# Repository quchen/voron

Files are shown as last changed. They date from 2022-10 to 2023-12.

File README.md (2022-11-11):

# Voron 2.4

This is my config for my 3D printer, a Voron 2.4r2, 250mm size.

For pretty (and not so pretty) pictures, look at buildlog.md.

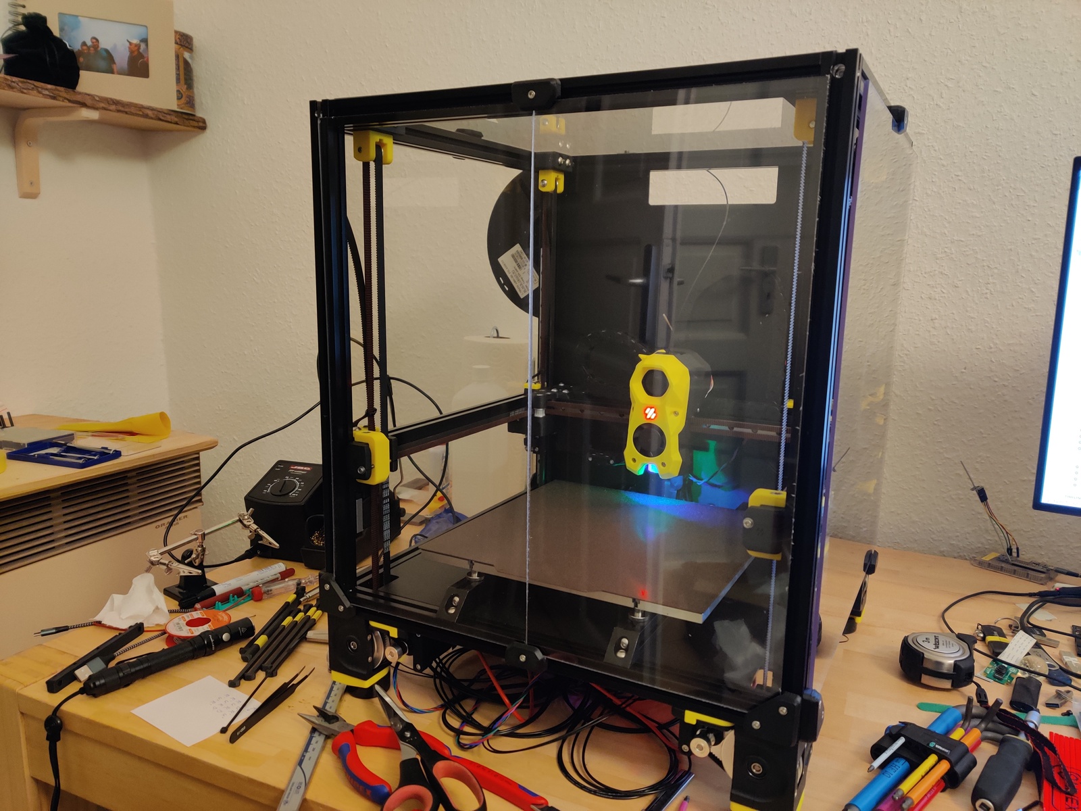
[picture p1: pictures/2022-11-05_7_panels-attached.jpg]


## Table of contents

- [config/](config/)         Printer configuration files.
- [manuals/](manuals/)       Assembly, circuitry, etc.
- [mods/](mods/)             Addons for the printer.
- [pictures/](pictures/)     Pictures for the buildlog.
- [buildlog.md](buildlog.md) Buildlog for everything I’ve done on the printer,
                             including time estimates.

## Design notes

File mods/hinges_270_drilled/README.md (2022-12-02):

https://github.com/VoronDesign/VoronUsers/tree/master/printer_mods/chrisrgonzales/270_degree_hinge

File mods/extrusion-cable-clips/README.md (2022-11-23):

# Extrusion cable clips

I use these to hide my motor cables in the back of the gantry.

https://www.thingiverse.com/thing:2246832

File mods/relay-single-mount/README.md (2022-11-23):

# Relay mount

This one was given to me by a friend. The holes in the relay PCB are too small
though so it doesn’t quite fit :-(

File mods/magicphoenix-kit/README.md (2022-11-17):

# MagicPhoenix Voron kit parts

Some custom parts for e.g. the breakout PCB.

https://github.com/MagicPhoenix/MPX-VORON-24R2-KIT/tree/main/Printed%20Parts

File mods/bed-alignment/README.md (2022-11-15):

# Easy bed alignment tools

Why didn’t I use those in the build!

https://github.com/VoronDesign/VoronUsers/tree/master/printer_mods/GadgetAngel/Bed_Support_Alignment_Tools

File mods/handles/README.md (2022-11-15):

# Handles for picking up the Voron

https://github.com/VoronDesign/VoronUsers/tree/master/printer_mods/jeoje/Sturdy_Handles

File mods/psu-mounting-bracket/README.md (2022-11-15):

# Meanwell 24V PSU holder

https://github.com/VoronDesign/VoronUsers/tree/master/printer_mods/aTinyShellScript/RS_PSU_DIN_Brackets

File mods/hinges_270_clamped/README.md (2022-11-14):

https://github.com/VoronDesign/VoronUsers/tree/master/printer_mods/AlexanderT-Moss/270-Clamping-Hinges

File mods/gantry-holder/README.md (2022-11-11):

# Gantry holder

These sticks allow hanging the gantry on the top of the frame. Useful to work at
its bottom, e.g. to change the gantry supports. They also ensure the gantry is
at the same height on all sides.

https://github.com/VoronDesign/VoronUsers/tree/master/printer_mods/tallman5/z-locks

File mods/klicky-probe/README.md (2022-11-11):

# Klicky probe

https://github.com/jlas1/Klicky-Probe/tree/main/Printers/Voron/v1.8_v2.4_Legacy_Trident/v1.8_v2.4_Legacy_Trident_STL

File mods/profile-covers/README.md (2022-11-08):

# Profile covers

- https://github.com/VoronDesign/VoronUsers/tree/master/printer_mods/chri.kai.in/20x20mm_Profile_Covers
- https://github.com/VoronDesign/VoronUsers/tree/master/printer_mods/filotto78/6mm_slot_cover

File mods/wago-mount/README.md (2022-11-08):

# Wago mounts

Not much to say. Wago clamps are cool.

https://github.com/VoronDesign/VoronUsers/tree/master/printer_mods/LoganFraser/WagoMounts

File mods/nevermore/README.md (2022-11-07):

# Nevermore

Don’t like cancer because of toxic styrene in your lungs? Lucky you are!

- Printed: Standard version (not XL)
- Git hash: 10ec5e9e80064c5ac2ecf3905a2cfe98cf476909 (2022-11-06)
- Git: git@github.com:nevermore3d/Nevermore_Micro.git
- Github: https://github.com/nevermore3d/Nevermore_Micro

# Official readme

Four parts; Plenum+Lid, and Cartridge+Lid.

Choose between regular and XL cartridge. XL is just 10mm longer, which can make
a big difference in air flow.

Choose XL for max carbon content and filter duration, and if you don't mind the
fan (200Pa+) has to run faster/noisier. You probably have to use pellets instead
of granular carbon too.

Choose regular if you have granular carbon and/or a weaker fan, and/or wish to
have a more silent experience. Regular also allows for somewhat higher airflow,
which could make a small difference compared to XL in chamber heat up times.

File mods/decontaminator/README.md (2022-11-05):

# Decontaminator

Wipes the nozzle before printing to remove all the gunk.

https://github.com/VoronDesign/VoronUsers/tree/master/abandoned_mods/printer_mods/edwardyeeks/Decontaminator_Purge_Bucket_%26_Nozzle_Scrubber

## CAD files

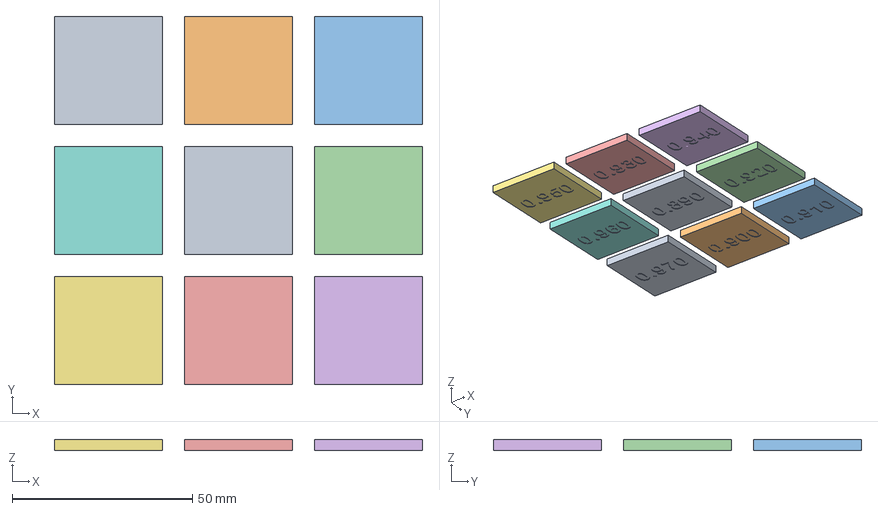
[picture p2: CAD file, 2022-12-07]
config/calibration/extrusion-multiplier-andrew-ellis.3mf
102.0 x 102.0 x 3.00 mm
EM_Cube-0.890.stl
EM_Cube-0.900.stl
EM_Cube-0.910.stl
EM_Cube-0.920.stl
EM_Cube-0.930.stl
EM_Cube-0.940.stl
EM_Cube-0.950.stl
EM_Cube-0.960.stl
EM_Cube-0.970.stl

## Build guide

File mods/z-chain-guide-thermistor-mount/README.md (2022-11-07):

# Z Chain Guide Thermistor Mount

https://github.com/VoronDesign/VoronUsers/tree/master/printer_mods/jeoje/Z_Chain_Guide_Thermistor_Mount

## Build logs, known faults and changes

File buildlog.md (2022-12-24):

# Voron 2.4 buildlog

This is a technical diary AKA buildlog of me assembling a Voron 2.4r2, 250mm
version.

I try to add annotations where I make mistakes, but in general it’s good to
double-check whether things I’ve described in a step are a good idea before
copying them.

# 2022-10-25

Package arrived. Got Pif parts in blue and yellow.

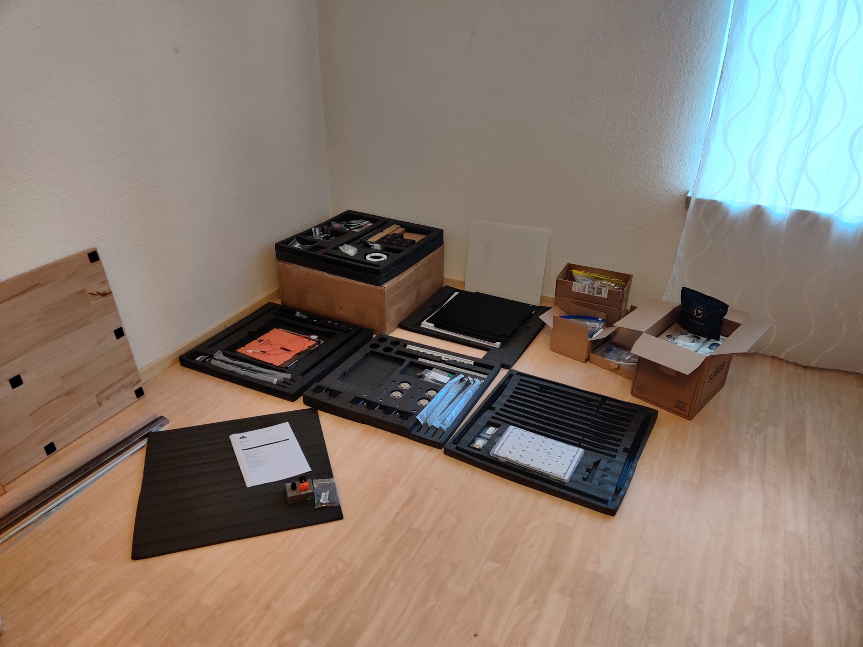
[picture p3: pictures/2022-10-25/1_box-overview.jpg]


Around 1m² of desk space cleaned, my trusty Prusa 2.5 went onto the gas oven
(turned off). Build area cleaned, let’s go!

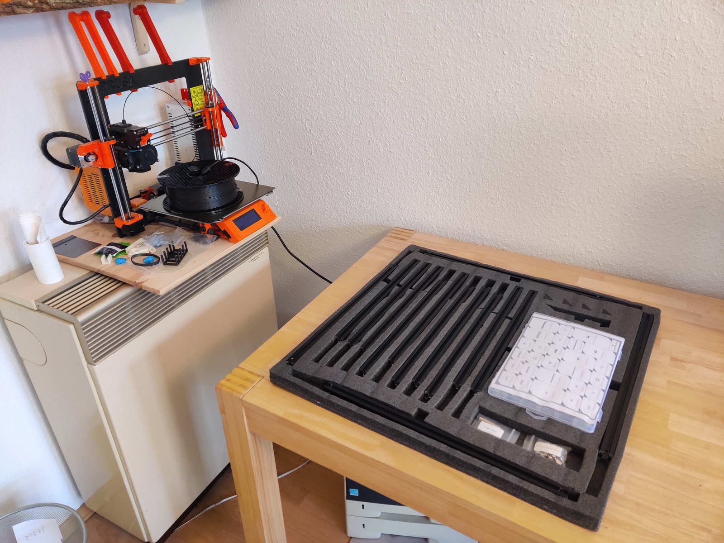
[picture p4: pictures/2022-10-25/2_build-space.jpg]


Time: 15min

Downloaded the build manual for Voron (and Stealthburner for later). Initialize
this Git repo. 5min

## Frame assembly

Extrusions sorted and labeled. 10min

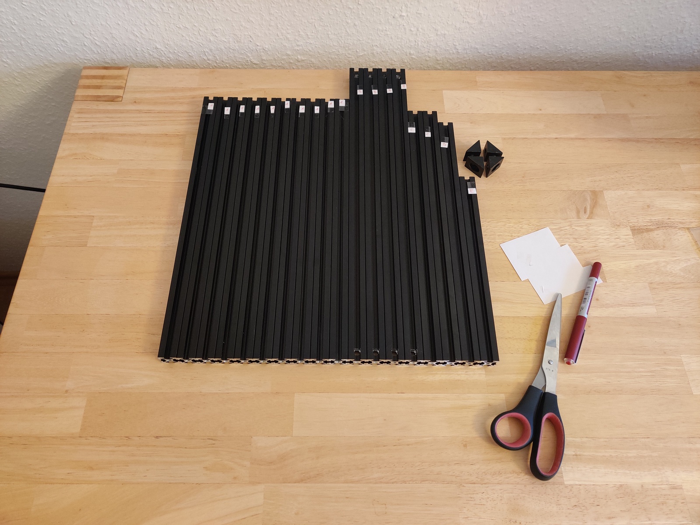
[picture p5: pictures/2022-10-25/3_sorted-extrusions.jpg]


Adding screws to A extrusions. I remember my friend telling me about the _frame
spring fasteners_ that they forgot initially. Time to open the
[MagicPhoenix manual](http://mpx.wiki/) as well! Yup, use (non-standard) frame
spring fasteners.

30min later, cube almost finished, forgot thread locker. Fuck. Anyway, time
to get the DIN angle for fine tuning, and the thread locker. Undo all the screws
again. Need to go boudlering though, and threadlocker would set a time limit on
assembly and squaring. Stopping frame assembly for now.

15min of unpacking linear rails, finding a suitable glass, and putting the
sliders into IPA. Now I will go bouldering for real, promise.

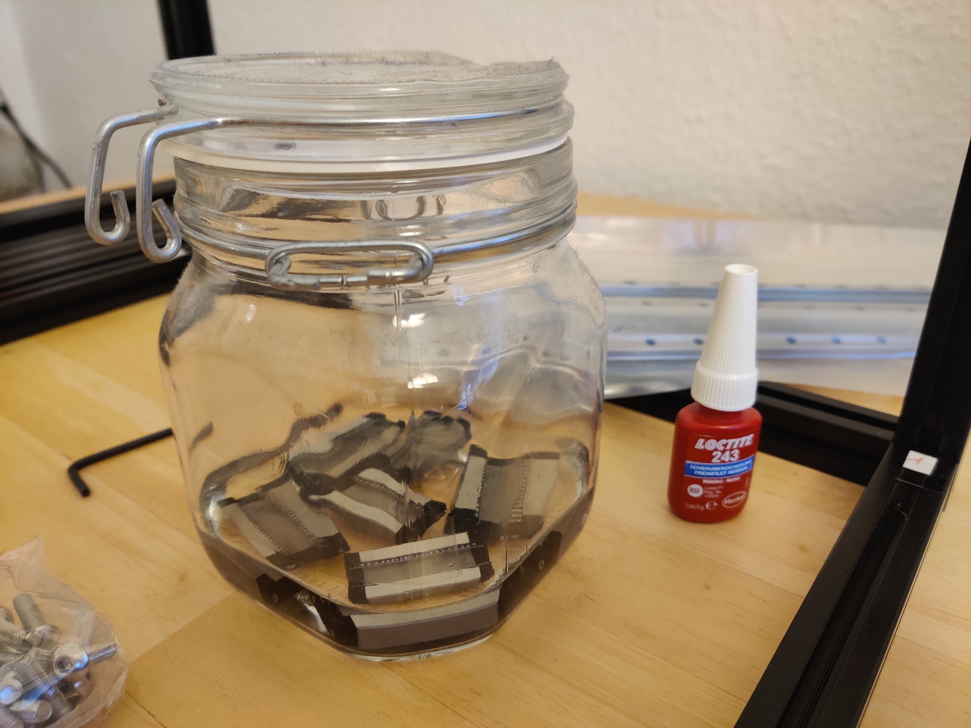
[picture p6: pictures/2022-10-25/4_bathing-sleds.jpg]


Time taken: 1h, total 1h15m.

Reassembled the linear rails while drenching them in IPA. Did not expect the
MGN9H to be _that_ hard to get on the rail, MGN12H is a piece of cake in
comparison. Some balls jumped out, reinserting them is super finnicky. Keeping
them on-rail in IPA for a bit longer, and will move them on occasion. Speaking
of movement, only one of the rails is good (sled moves under its own weight),
the rest is average, except for one of the MGN9H, which is quite stiff. Maybe
upgrade to Hiwin later (for a hefty premium …). 20min for this.

Another 45min later, the frame is fully assembled, and all corners are
electrically connected (diamond filing the contact surfaces). Used a DIN norm
angle to make sure the mechanical assembly is flush. Upper/lower Diagonals are
all 579mm, left/right/front/back ones 594mm without further adjustment. Kudos
to the precision work by MagicPhoenix! Used my DIN angle to check for 90°; most
angles are perfect, some are a tiny bit off so that I can
audibly-but-not-visibly move the angle. Good enough.

I decided against using threadlocker for the frame, because Loctite cures in
around 10-20min, which would not have let me adjust the screws if things
hadn’t gone to plan. Might add Loctite later screw-by-screw when more things
hold the frame in place, but only if problems occur. Screws are tight so that
when I use the hex key with the worse lever, my finger hurts when turning them.

Installed the heat bed rails by estimating the center of the bed with a tape
measure, and going from there with the caliper. Distance between the extrusions
is 130mm±<0.2mm, way more accurate than I need. I do have an offset by 0.5mm to
the left though, which I will worry about when installing the bed, which should
give me much more practical guidance. **Note from the future:** there is a
[simple alignment helper mod][bed-rails-alignment] that would have made this
much easier.

[bed-rails-alignment]: https://github.com/VoronDesign/VoronUsers/tree/master/printer_mods/GadgetAngel/Bed_Support_Alignment_Tools

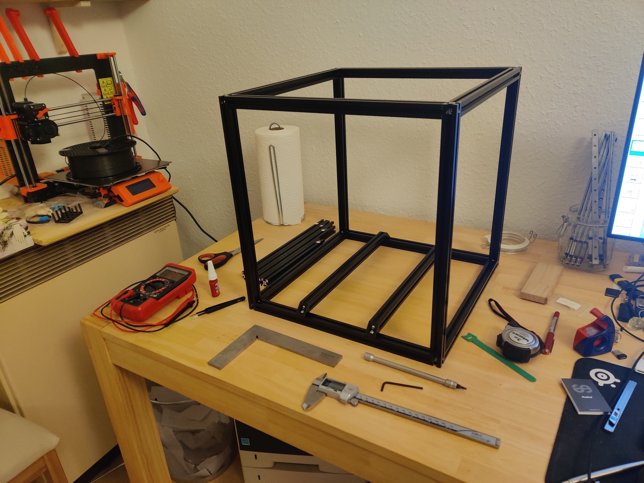
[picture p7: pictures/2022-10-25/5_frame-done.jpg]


Time taken: 1h45m, for a total of 3h so far.

# 2022-10-26: Frame and gantry

## Z linear rails

Spent 15 minutes greasing the rails with standard grease. It’s quite hard to get
it in there, the syringe tip didn’t work (inject it from below through a rail
hole). Just made a little mess and hoped enough would be on the bearings.

The next 45min I installed the rails. I got one nut the wrong way round; it’s
not noticeable but _I know_. It’ll be my secret. Nothing special here, just
juggling with Loctite hardening, and aligning them quick enough. The plastic
rail adjustment clamps are a blessing. Oh and my Yubikey is 3.5mm thick, so I
used that as a spacer for the gap at the bottom of the Z rails. **Note from 50h
in the future:** A bigger gap makes it easier to insert covers later. There is
zero need to have the carriages go that deep. Make it 5mm or even 10mm!

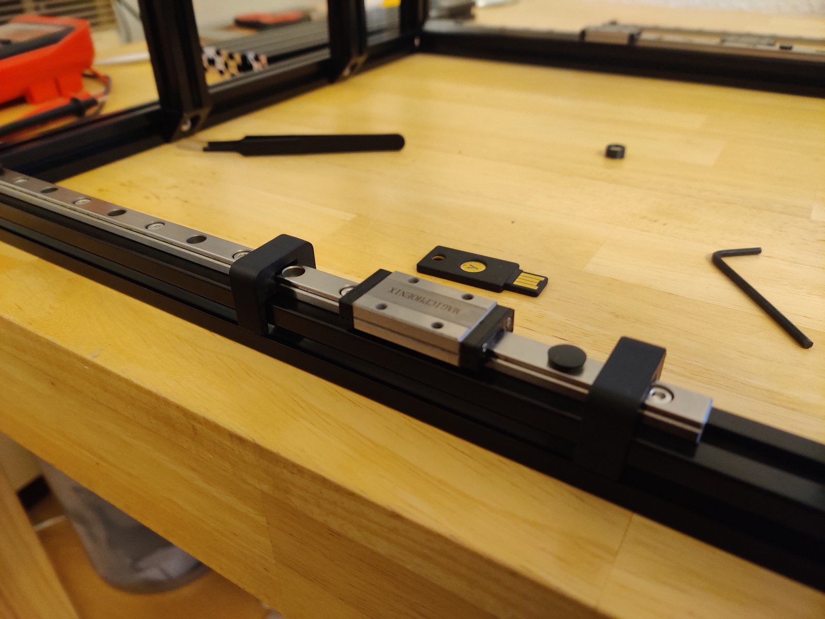
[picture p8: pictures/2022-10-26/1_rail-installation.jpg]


# DIN rails

15 minutes for installing the floor and DIN rails. Initially I installed the
rails parallel to the bed rails, but they actually have to be perpendicular.
Takes a minute to change that though, so no problem.

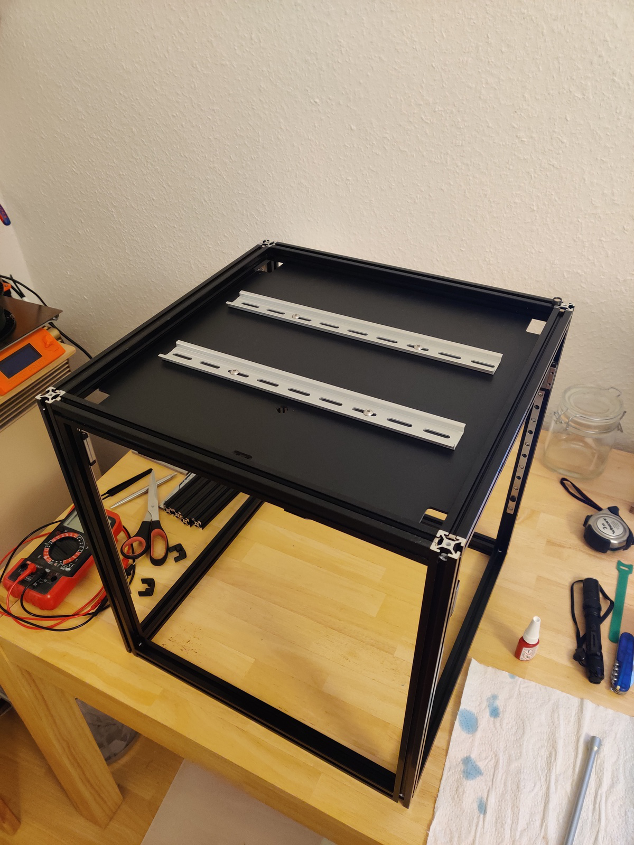
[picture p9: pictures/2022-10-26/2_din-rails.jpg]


The next 30 minutes were pure bliss: heat inserts. It’s amazing. I hope there
are many more. 250 °C on the soldering iron, slowly pushing it in, then flushing
the surface with a flat piece of plastic for a couple of seconds. All inserts
are _perfect_. I’m proud.

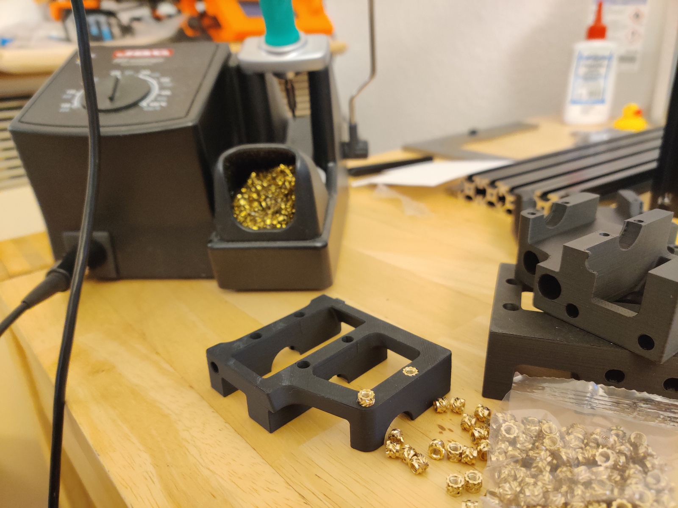
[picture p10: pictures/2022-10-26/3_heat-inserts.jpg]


The first foot for the frame to stand on took 45 minutes. A couple of small
mistakes were easy to remedy, namely I screwed the foot onto the wrong side of
the frame, and also I forgot including the M5 nut for the plastic foot’s foot to
be fastened to. Neither took more than a minute to fix.

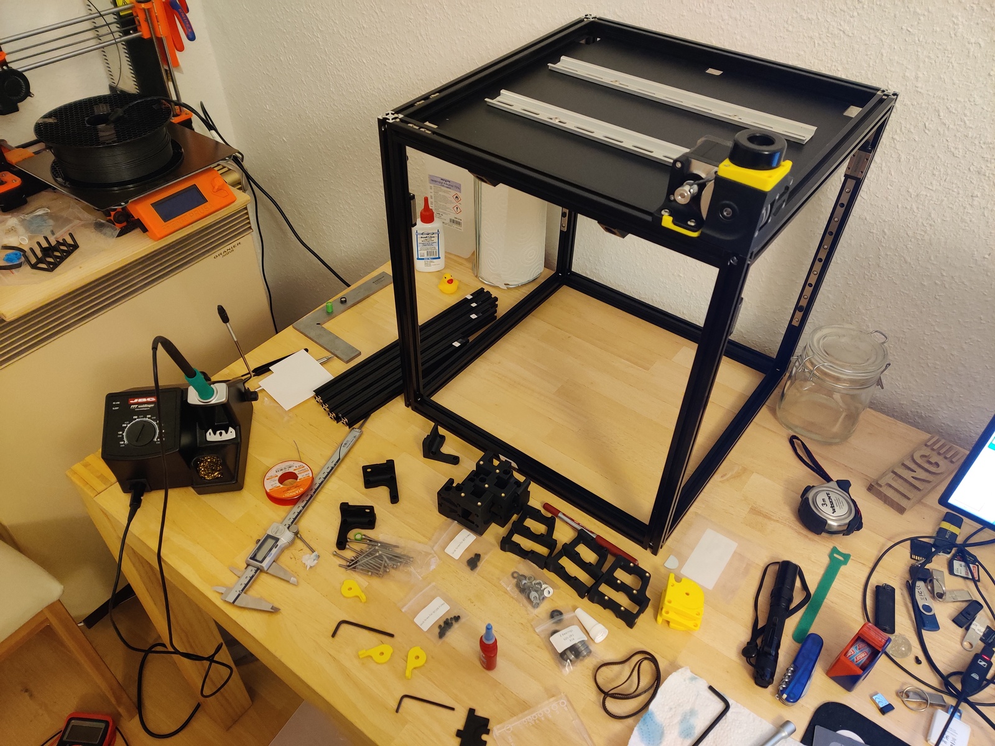
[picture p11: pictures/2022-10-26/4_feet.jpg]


Eyedler are super easy to build and install, maybe 20 minutes. I don’t have a
ball hex key though, so I won’t be able to fasten the belts thanks to their
design.

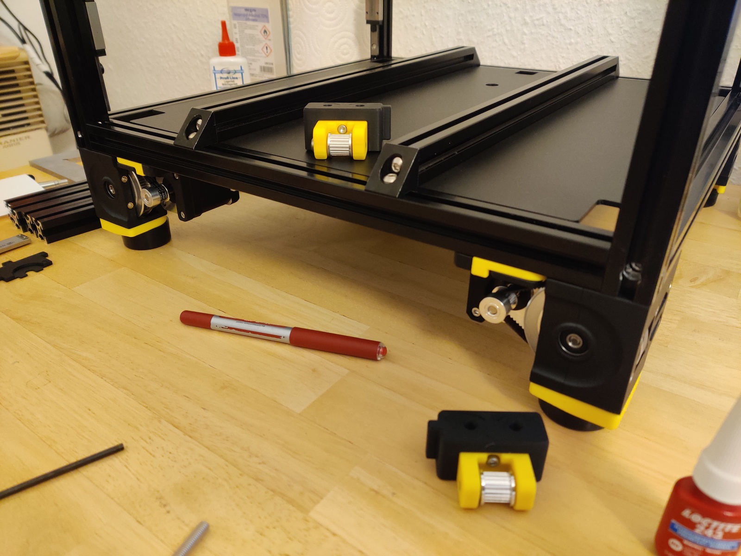
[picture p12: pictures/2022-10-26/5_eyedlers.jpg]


2h30m Session; the frame is now super done, for a total of 5h30m.

## Gantry (3h30m)

Gantry time! At first I thought Pif had forgotten the B idlers, but the parts
just look different, and everything was there. A couple of heat inserts, lots of
screws that I don’t fasten yet because I don’t know whether I should wait for
the wedding with the frame or not.

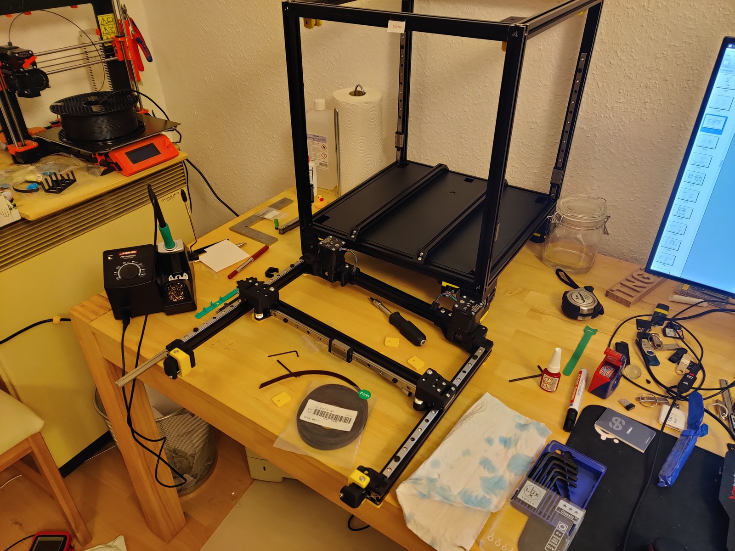
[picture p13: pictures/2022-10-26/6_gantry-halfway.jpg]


This is also when I noticed the reason my Loctite doesn’t yield drops without
extensive begging because – you won’t believe it – it was empty. Visited my
friend to get backup, and also some useful tips for the coming steps. 60 minutes
so far.

2h more gantry assembly. Lots of screws are only tightened a bit, the goal being
joining it with the frame and then working out where everything should be.

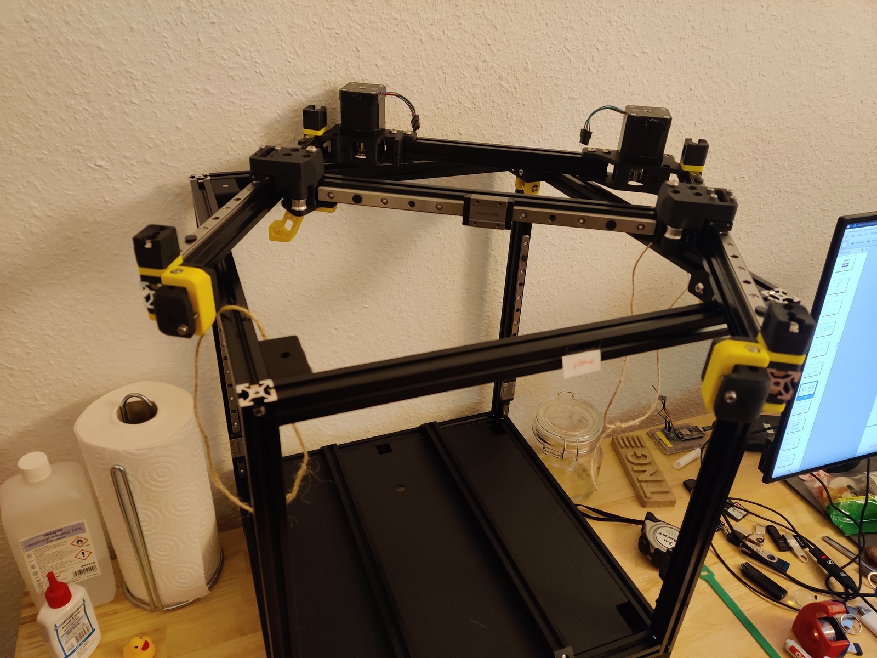
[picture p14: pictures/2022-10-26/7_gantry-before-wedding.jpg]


It’s now 0:20, the gantry is done, time for the wedding!

0:40 Wedding is done, but I noticed I misunderstood the Z belts: I should
already have added them on lower clamps. That’s going to be finnicky; I think
it’ll be easier to take out the gantry again, fixing the belts, and while I’m at
it tighten some screws. I’ll really have to remember to double-check all the
gantry screws later.

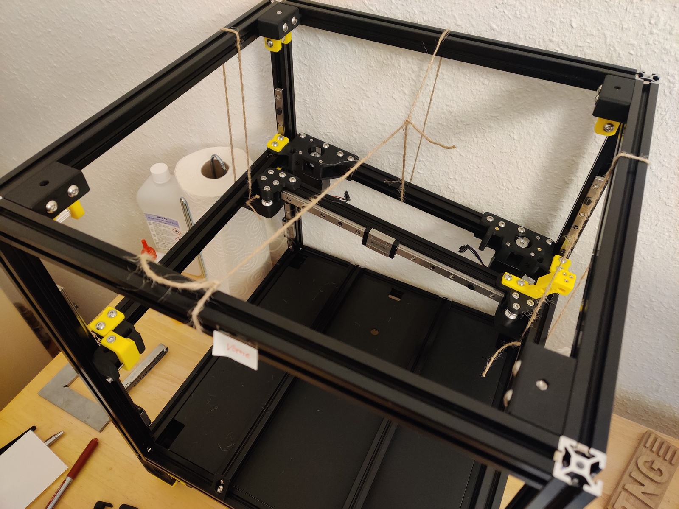
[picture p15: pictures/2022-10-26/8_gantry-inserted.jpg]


The gantry took me around 3h30m so far, for a total of 9h assembly at this
point.

# 2022-10-27

## Z locks

A cool mod I was recommended is [Z locks][z-locks]. It’s one of those that you
miss when searching for super cool mods before building. It holds the gantry in
place so you can access it without taking it out again. Printed six of them on
the Prusa in less than 2 hours while I was working. The fit is quite tight so
it’s quite secure even if you work on the printer or bump into it. I also cut
the 5m×9mm belt into 1.1m strips of equal length for the Z axes (the manual said
at least 1m for the 250mm printer, so I won’t have usable leftovers anyway).
15min.

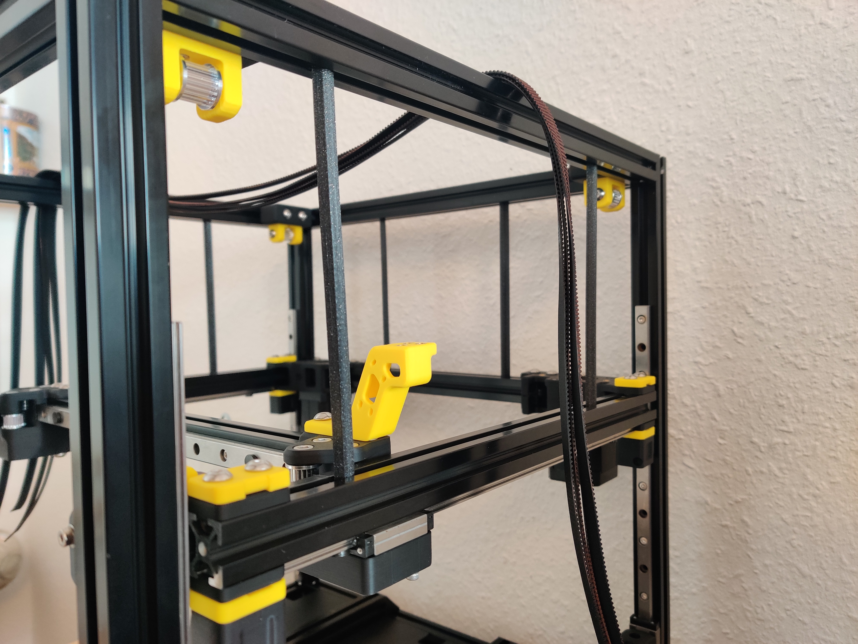
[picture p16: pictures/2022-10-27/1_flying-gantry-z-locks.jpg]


[z-locks]: https://github.com/VoronDesign/VoronUsers/tree/master/printer_mods/tallman5/z-locks

The 15min bring the total time to 9h15.

## Belting (2h)

30min for inserting the Z belts. I cut them 20cm too long, the »minimum« of 1m
from the manual would still have had 10cm slack as it turns out. This step is
much easier with the whole thing laying on its back; the Z locks are super
helpful, highly recommended.

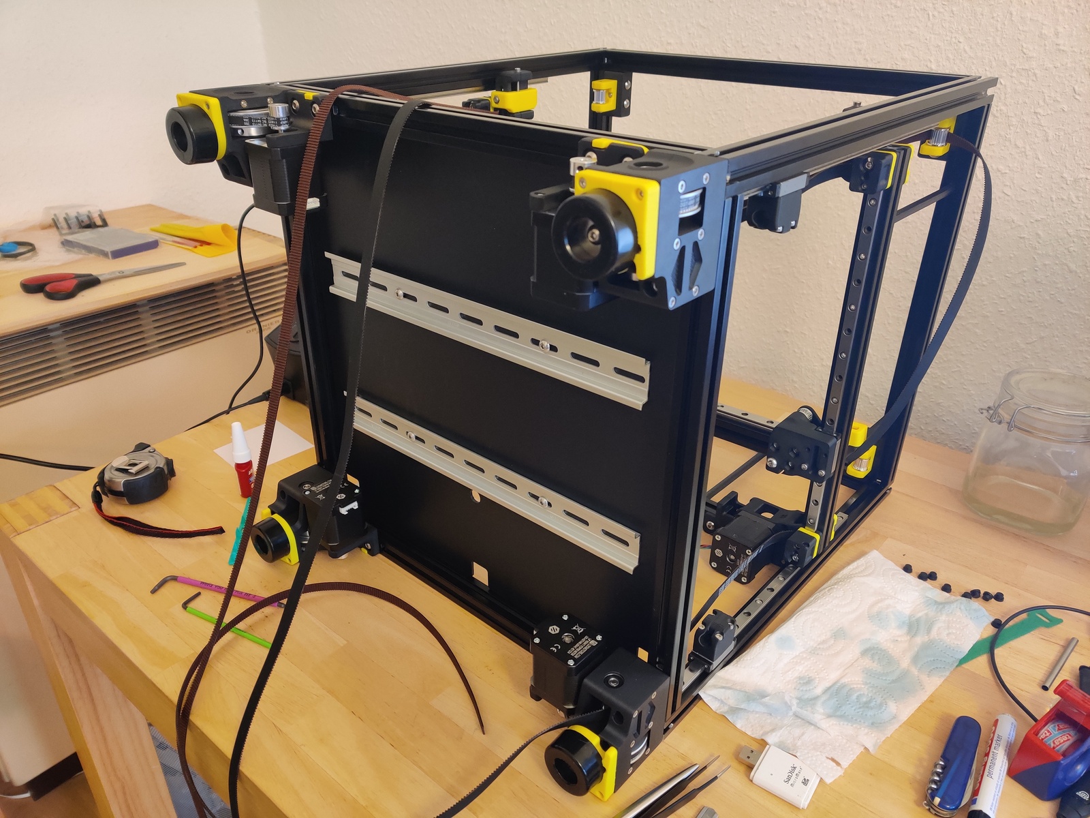
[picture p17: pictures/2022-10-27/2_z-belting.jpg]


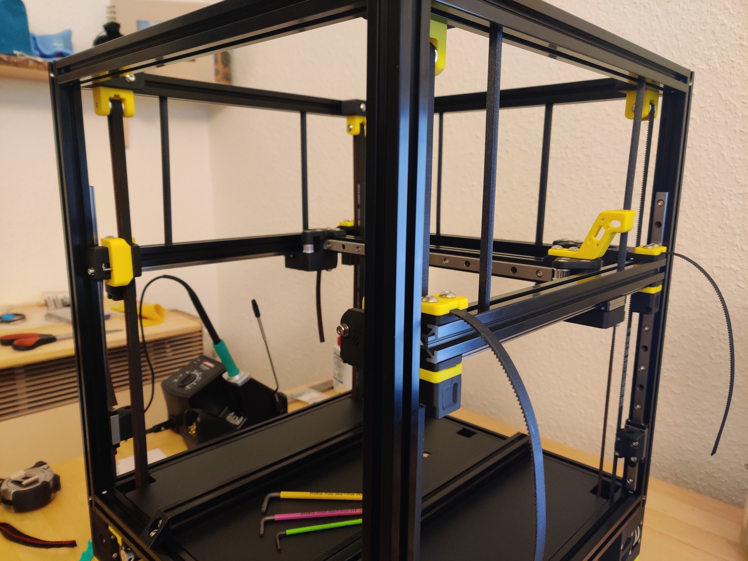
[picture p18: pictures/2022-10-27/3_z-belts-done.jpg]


Another 30 minutes later, the A+B belts are done. Some parts are quite finnicky,
but this is also what made it great fun for me, because there was always some
smart way to thread even the bendiest needles.

Alright, what’s next in the manual, ah yes, both belts must have the same
length, because that’s important for tensioning, symmetry, and stuff. Ah yes,
the design is also built in a way that despite both belts taking different
paths, their lengths match. Wellllll then, I guess I’ll take them out.

30s later, 30min of belting undone. At least I know how to thread them now. Cut
them to equal length to the tooth.

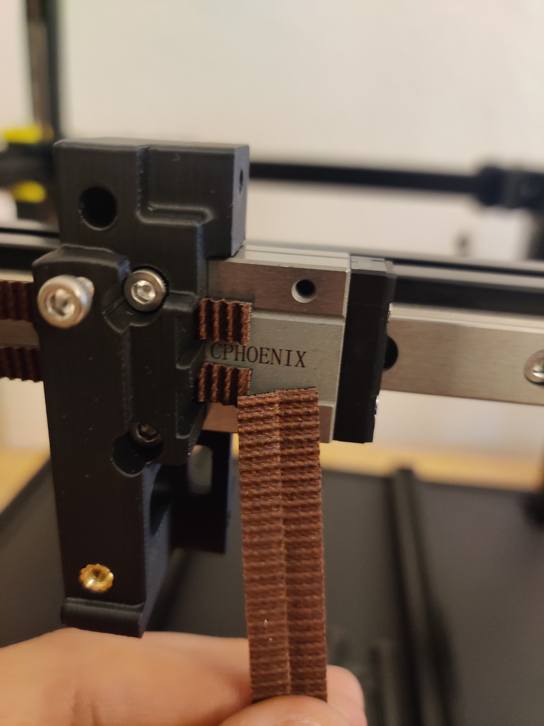
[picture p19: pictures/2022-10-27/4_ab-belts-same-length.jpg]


30 more minutes to insert the belts again. I was faster than the first time, but
filled the remainder of the time taken with playing around with the carriage.
Fun was had.

One thing I noticed is that the long M3x40 screw holding the A+B belt clamps
together on the carriage was too long; I used a M3x30 instead, matching the one
in the lower part. The lower one has to leave space for a hall probe magnet, but
still I’m not sure why the top is longer.

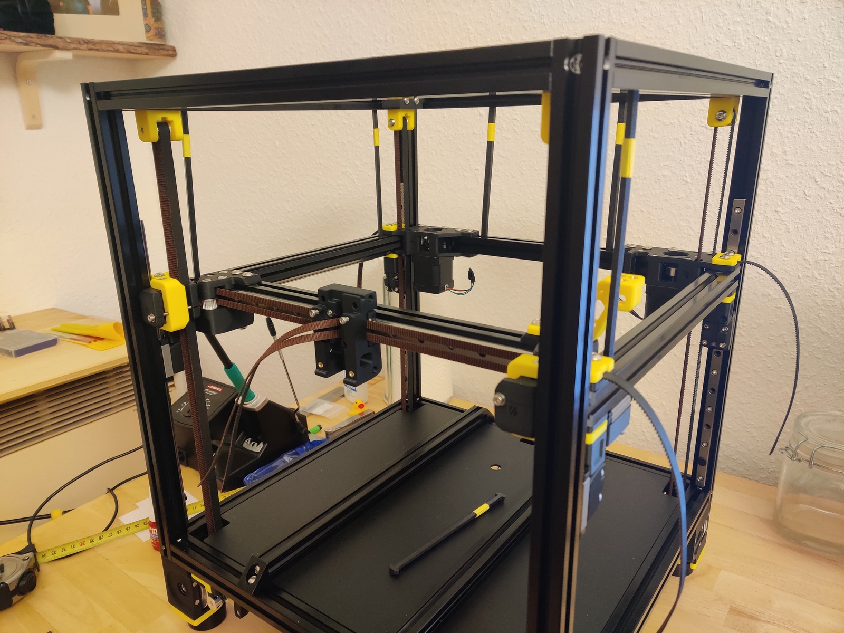
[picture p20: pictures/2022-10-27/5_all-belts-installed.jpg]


Turns out the machine is already deracked, cool! The carriage moves in Y
direction with constant resistance, with no X drift along the way, and hits the
left end right limits simultaneously. The advice of a friend is to take a look
at the [gantry squaring guide by Andrew Ellis][gsq], which features a couple
more steps, but also assumes wiring for many. It looks like a (chapter from a
much more extensive) great guide that I’ll revisit at a later point.

[gsq]: https://ellis3dp.com/Print-Tuning-Guide/articles/voron_v2_gantry_squaring.html

Oh, plus five minutes to tension the gantry bolts, almost forgot! And lol quite
a few of them were _loose_.

Taking some reading, playing around, and writing this text into account, I’ve
spent 2h on the whole belting topic, with a total of 11h15m so far.

# 2022-10-28 Print head, part 1

## Clockwork (1h30m)

More heat inserts, yippee! Although I must say the design is much less friendly.
Some inserts had shallow sockets so the soldering tip penetrated the plastic,
some were hard to reach without melting other parts. None of the mistakes I made
are visible from the outside though, and even if they were they’re very small.

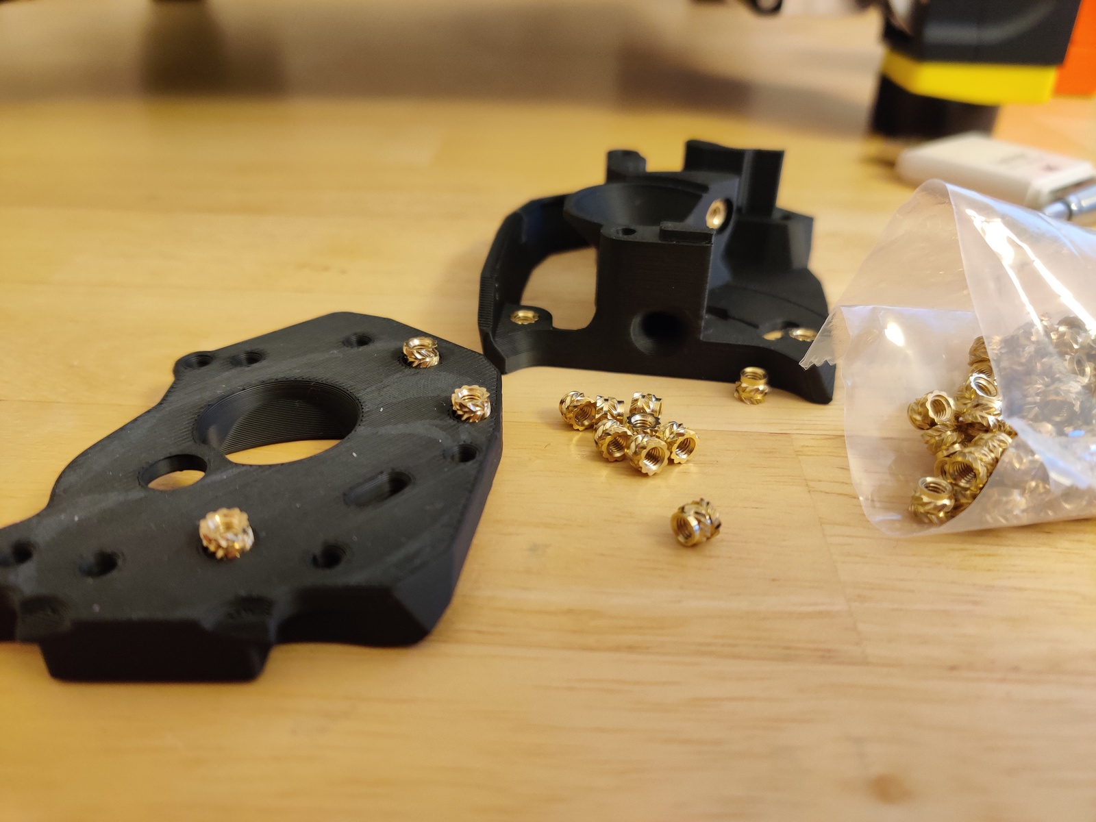
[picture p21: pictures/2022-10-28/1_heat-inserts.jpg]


The big gear is supposed to not touch plastic; I therefore moved it inwards as
much as I could. The cost of this is reduced overlap with the driving motor
gear, but we’re talking about less than a mm here on a motor that does not
require much power anyway; it drives filament after all, not a ship’s propeller.

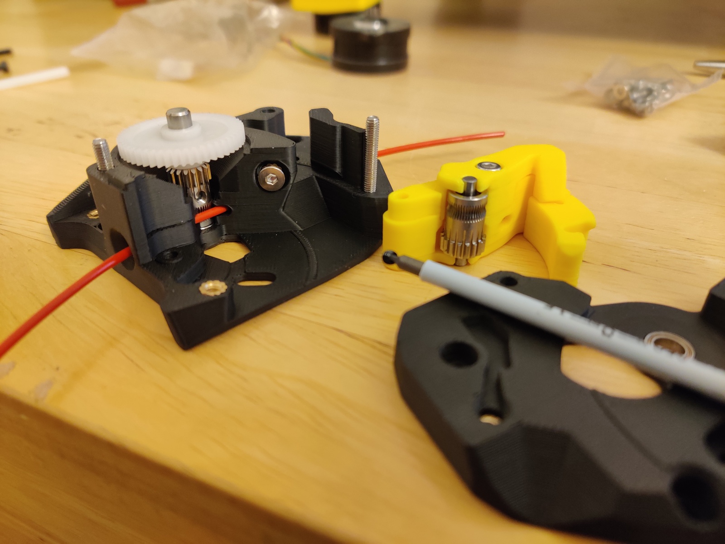
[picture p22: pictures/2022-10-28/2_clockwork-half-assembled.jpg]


I lubricated the passive extruder gear with trusty Traxxas 50k, a silicon-based
greased that is friendly to plastic, as my collection of Rubik’s Cubes can
attest to. Alignment of parts was pretty easy. I deviated from the manual by
securing the closing latch with a M3x8 SHCS (does fit) instead of M3x6 FHCS
(does not fit) screw.

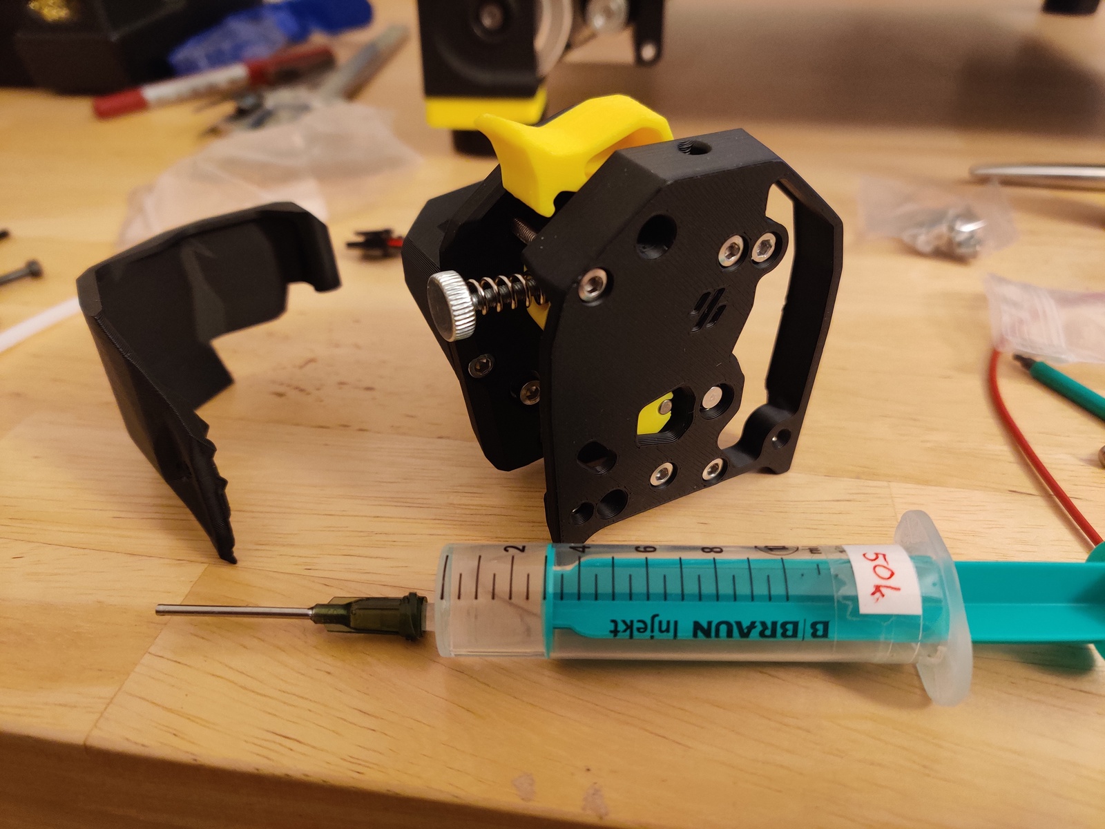
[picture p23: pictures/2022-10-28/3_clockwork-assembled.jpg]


This step took 1h30m. I no longer wonder why it’s called the clockwork, because
everything is hard to reach and see. Maybe also the big gear. Anyway, 12h45m
build time so far.

# 2022-10-31 Print head, part 2

## Stealthburner (1h30m)

I added the hotend; the orientation is such that the beveled end is facing the
front panel. Cable routing required some small amount of force; orienting the
heater makes the cables fall into place more naturally. I had to use the smaller
SHCS M3x8 screws from the hotend bag, the heads of the main kit were too big and
would not fit the four holes in the plastic part. I cut the PTFE tube to stick
out 10.9mm (should be 11mm), but I think that’s close enough. The socket is
designed to hold this whole part on its own, at least enough for adding the
front later. No zipties had to be used to temporarily hold it in place.

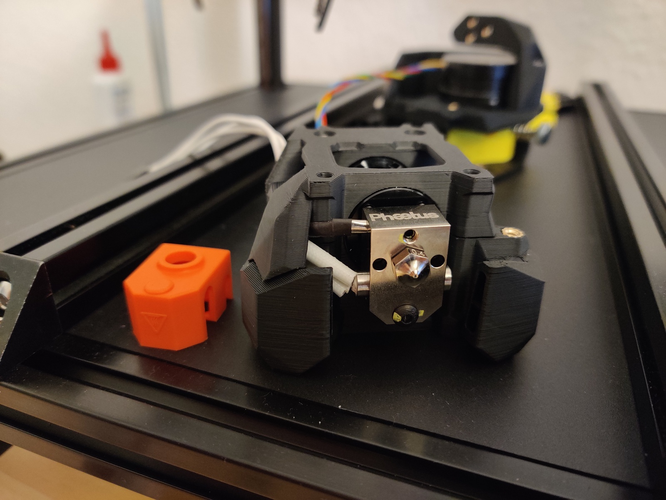
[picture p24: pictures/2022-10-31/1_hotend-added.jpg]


Up next, LED insertion. Smooth sailing; the cables were a bit long, but easily bent into the plastic gaps.

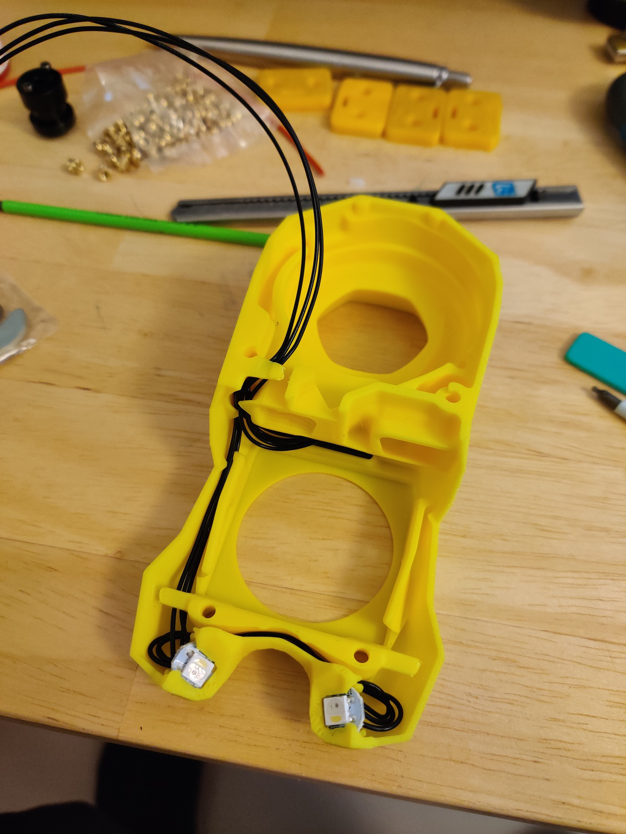
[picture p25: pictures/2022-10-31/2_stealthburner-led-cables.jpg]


Taking apart the part cooling fan was a bit tricky, but pushing the latches with
my tweezers won after a couple of attempts. I cut off the ears with side
cutters, and filed them down to be somewhat flush. The part doesn’t have to be
super flat, there is some tolerance in the SB head. When staring at the fan from
the front long enough it might not be 100% centered, which might be due to the
non-perfect flush-sanding, but I’ll leave this for a future modding session.

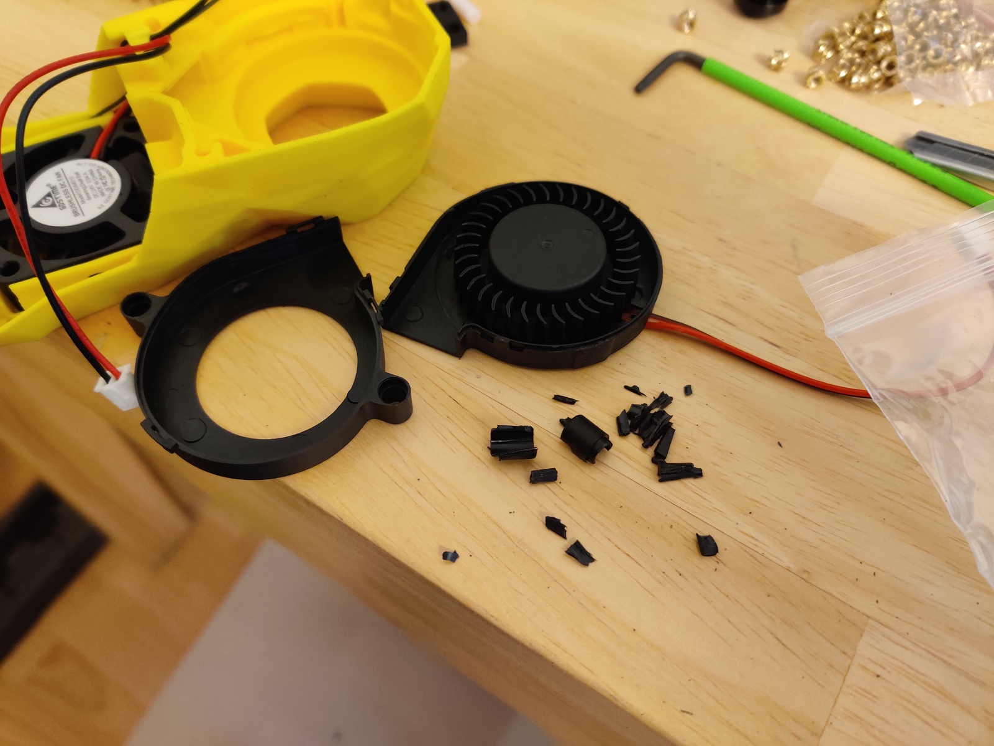
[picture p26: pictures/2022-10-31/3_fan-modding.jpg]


The Klicky probe is easy to install; I did not notice the right way to route its
cable is straight up past the belts and then into a groove made for just that,
and considered just routing it outside. The Voron devs thought of everything it
seems!

**Note from the future:** The Klicky holder isn’t parallel to, well, anything.
Make sure when checking the Klicky later that it’s parallel to the bed,
otherwise the effective switch height will be different, which gave me nozzle
calibration issues bad enough to visibly scratch my bed with the nozzle.

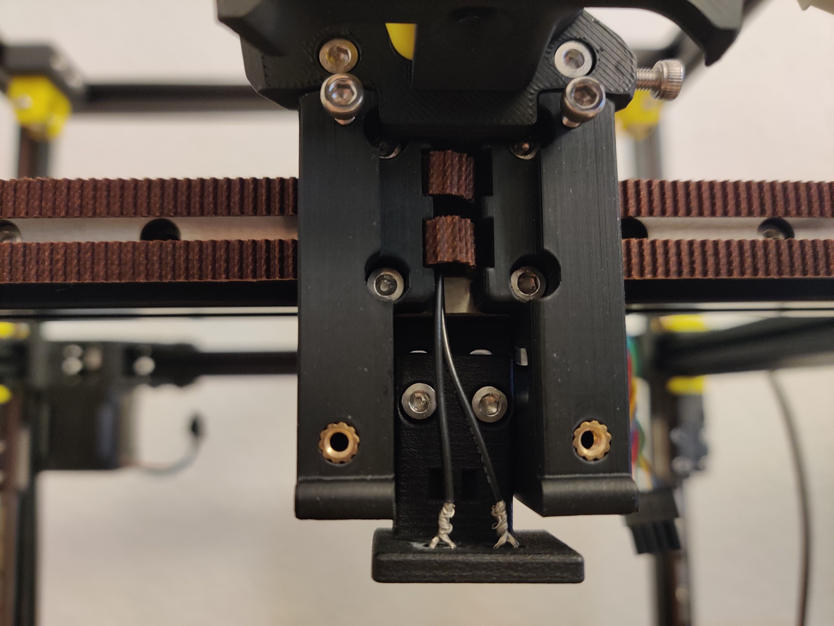
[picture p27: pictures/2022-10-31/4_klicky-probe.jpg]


Bolted on the front, and mechanical assembly is done! It looks like a Voron now!

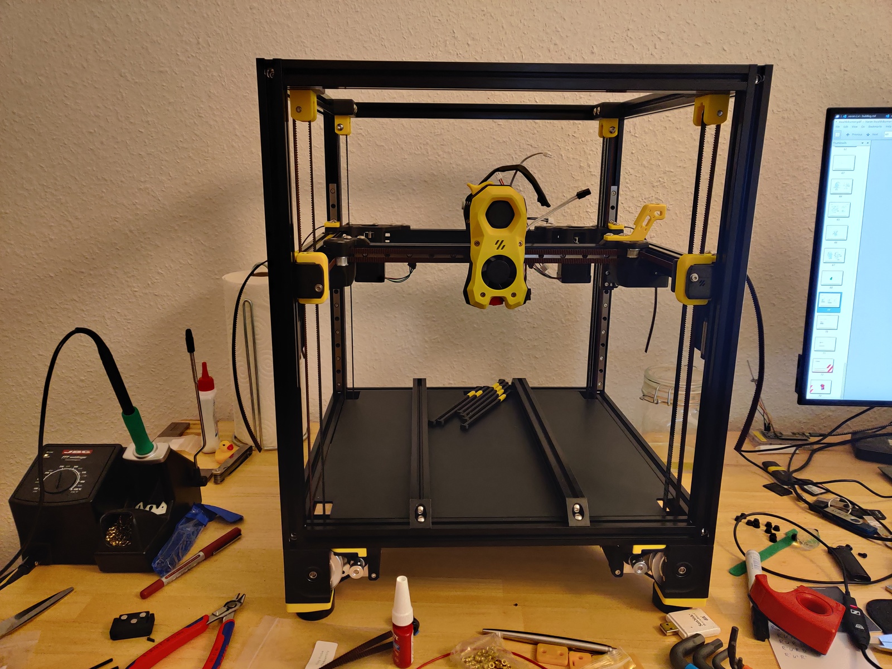
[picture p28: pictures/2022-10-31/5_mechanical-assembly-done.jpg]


With 1h30m in this session, I spent 14h15m on mechanical assembly.

# 2022-11-01 Kickoff for wiring

## Assemble mounts (2h30m)

Raspi, Octopus, SSR: just screwed on the holds without washers. Uneventful. The
power switch is hard to put on the frame when the switch/inlet are put in, so I
had to un-screw it, mount it on the T-nut, and reinsert it. Sexbolt is super
easy to assemble; I added some Traxxas 50k to lubricate it, and of course used
Loctite. The main issue was with the big PSU, it just wouldn’t fit on the DIN
rails. I found out I could simply unscrew the DIN rails, which have a couple of
centimeters play left and right, and retighten them at a more useful distance.

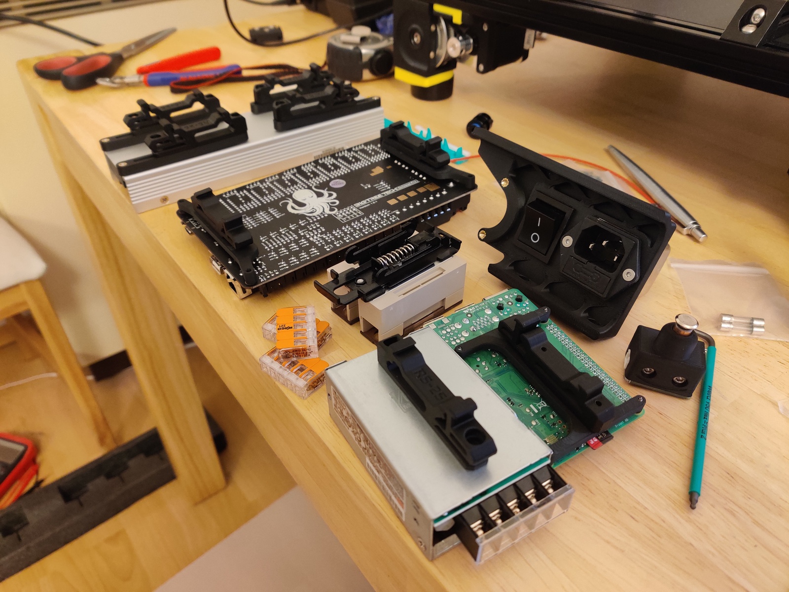
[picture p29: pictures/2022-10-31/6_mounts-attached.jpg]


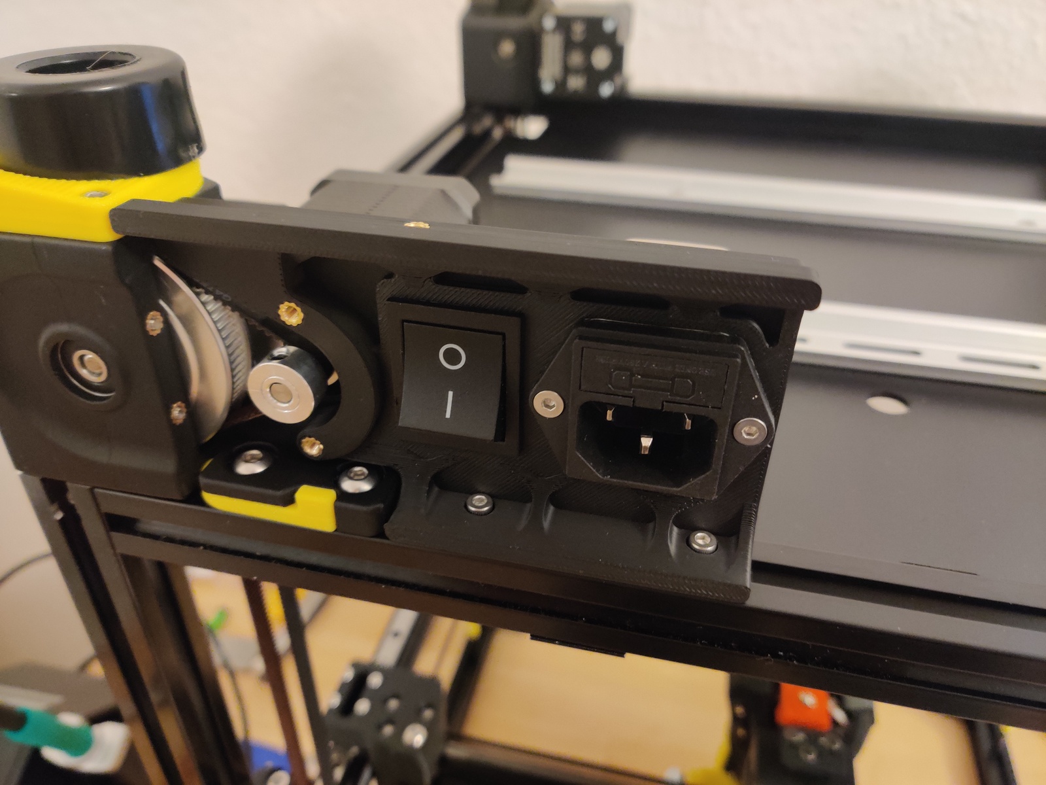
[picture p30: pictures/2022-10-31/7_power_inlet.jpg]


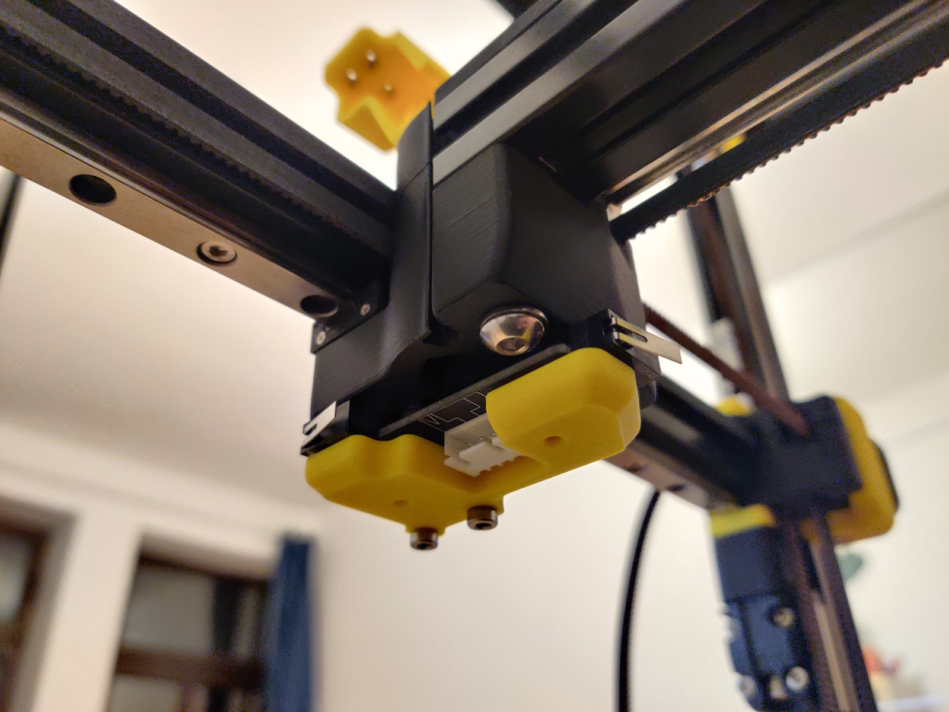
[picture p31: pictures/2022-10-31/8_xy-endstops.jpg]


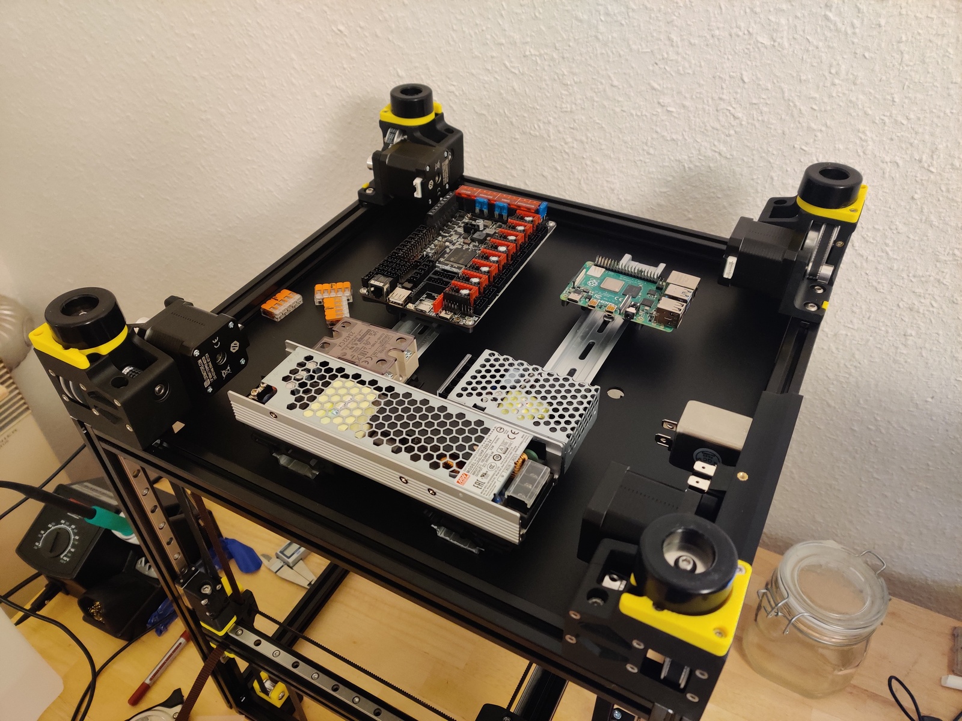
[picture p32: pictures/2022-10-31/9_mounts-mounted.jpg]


2h30m so far, 2h30m for electric assembly, and total build time 16h45m.

## Octopus setup (30m)

For the Octopus, I first removed all jumpers, as the manual says. I then set all
fans and the probe input to 24V and added the drivers. Should I fry the board,
here are pictures of the electrical setup for later reference.





The gap in the drivers line is because motor 2 (0-based indexing) has two slots,
so I’ve skipped motor 2.2 and only used 2.1. **Note from the future:** thsi was
incorrect, and fixed a later step! There are 8 driver slots for 8 drivers, but
there are 9 motor slots, and the driver in position 2 of 7 (0-based) has two
motor slots that can be driven by the same driver. It is valid wiring, looks
awkward, and would at least not fry the board if done this way.

This step took me around 20min, but I also watched a video on how to assemble
the heatbed which I still have to add, bringing the electrical part to 3h, with
a total build time of 17h15m.

## Wiring AC, part 1 (1h15m)

Wiring is a pain! I spent 1h15m on trying to figure out the pieces of shit UK
clamps, only to realize that I bought Wago clamps for exactly the same purpose.
I didn’t have the mounting clamp handy, so I printed it in PLA, to be replaced
by an ABS version later. I’ve opted for the extrusion mount (instead of the
DIN-based one) because it seems easier to use, at least until I know where the
wires are running, and where I have space left on the DIN rails. Since I’ll
exchange the PLA part with ABS later anyway, I can use that opportunity to
decide for the other design, should I want to.

4h15m on electrical thus far, total build time 18h.

## Intermezzo: heatbed (30m)

I’ve never glued on a heatbed, so here goes nothing! Cleaned the cast aluminium
plate with IPA until _nothing_ was visble on the cloth anymore, then peeled off
a couple of cm of the adhesive cover. Put the entire magnetic sheet on the
surface for alignment, with the partially peeled off cover providing some
resistance so the glue doesn’t stick already. When I was happy with the
alignment (each side a bit wider than the actual aluminium, to be cut off
later), I massaged inside out, with my soldering tip holder plastic piece. It’s
quite the utility, doing this and also helping me with inserting heat inserts
flush! After 15min I was done, no bubble to be seen. I put the result upside
down onto the foam packaging I got the printer parts in, so that the weight of
the plate can help with a bit of pressure when curing.



Next step, the heat sheet. Pretty much the same procedure, same alignment and
partially peeling off tricks, same 15min.



I must say, I think I did this quite well for the first time. No bubbles to be
seen, very symmetric. Since this wasn’t really part of electrical assembly, I’m
leaving that total at 4h15, but the total build time increases to 18h30m.

## Wiring AC, part 2 (1h30m)

Meanwhile, the Wago mount clamp has finished printing, time to continure wiring!
Up to a couple of cables that were too short and constrained my choice of
location for some of the parts, everything went smoothly. Thank you Wago.

Turned on power, the switch works, and the green status LEDs of the PSUs light
up as well. 30min (total wiring 4h45m, total 19h).



For the DC circuit, it looks like the cable to connect both V- of the PSUs is
missing. I’ll have to remember adding this later!

The cable routing is a mess, I’m not sure the cable ducts would be an
improvement though, since space is super limited. And it’s going to get much
worse once the printing wiring is added!

A couple of things are still missing in the power circuits:

1. Grounding the frame and the DIN rails
2. Connecting the V- outputs of both PSUs

Other open questions include what the purpose of the BED_POWER connector on the
Octopus is for, since I thought I was using a SSR for providing power from DC,
controlled via the BED_OUT terminal.

Here’s a picture of the current state for your enjoyment.

1h more spent on wiring, so we’re at 5h45m electrical, and 20h total.



# 2022-11-01: fixing mistakes and power wiring

In the last session, I made a couple of mistakes.

1. I misunderstood the bed connectors of the Octopus. The correct way of wiring
   is that the board routes `bed power` to `bed out` based on a Mosfet, and
   controls heating this way. **Note from the future:** the bed in/outputs
   aren’t needed, because I have a separate relay that a thermal output can
   handle. The bed in/out are only needed when heating the bed directly over the
   Octopus.
2. I also misunderstood `motor power`. This is only necessary if the bed power
   is a different one than the board power. In my case, both are 24V (and not,
   say, 48V for the motors), so I can just leave the `motor power` unconnected.
   The jumpers next to the drivers near the edge are in _use board power for
   motors_ position anyway. This wasn’t electrically wrong (phew!), but needed
   additional cables to connect the `motor power` connector, so out it goes. In
   a future mod, since I’m using the huge relay anyway, I could get rid of both
   the bed connectors, and route some thermal regulator pin to the relay
   directly, since it doesn’t need bed power for switching. The setup right now
   is the one one might use when powering the bed directly from the Octopus
   (with 24V).
3. The gap between the drivers isn’t necessary. There are 9 motor outputs with
   motor driver #2 (0-based) having 2, but the drivers themselves are gap-less.
   I rearranged them neatly. The gap will instead be between the motor
   connectors.
4. In general, I looked at the docs for the Octopus _1.x_, and not the Octopus
   _Pro_. Oops. Not too bad at the moment, but would have me scratch my head
   later when looking for specific pinouts.
5. I did not ground the DIN rails or the metallic frame. I’m literally betting
   my life that none of the live wires touches the frame.
6. The V- outputs of the PSUs weren’t connected. They are now. Since I didn’t
   have thick enough black/red cables, I tore apart a power socket cable, and
   used brown/blue instead. I’m sure this violates some DIN, ISO or geneva
   convention rule, but what can I say, I’m just a theoretical physicist, and I
   promise to fix this later™.
7. The Sexbolt had a bit too much resistance on the piston, making me afraid it
   would get stuck in a hot chamber and maybe with time. I took it apart again
   (scratching out the Loctite, ugh), applied a very thin layer of Traxxas 50k
   that I wiped off again because it was maybe too stiff, applied new Loctite,
   and reassembled. The piston now moved under its own weight, and also during
   gentle shaking. Good enough! (Counting the 30m for this towards total, but
   not electronics, time.)



Time for a last check of everything before flipping the power. There will either
be smoke, no smoke but nothing useful, or I will be able to connect to Mainsail
(which I previously installed on the Raspi).

Flick.

LEDs begin to shine. No smoke, no noise.



Mainsail! Woohooo!! (After connecting the LAN cable. I’ll set up Wifi for the
Raspi next.)

The next steps were spent fiddling with a hub that I haven’t used in ages. My
desktop doesn’t have Wifi, I forgot adding Wifi credentials on the Raspi, and my
laptop doesn’t have its SSH key authorized by the Raspi.

Once connection was established, the dashboard wouldn’t appear because some
necessary-and-essential fields, such as the MCU, the kinematics, and motor pins
weren’t specified. I used dummy values copied from an example config to quiet
the errors.

It then could not connect to the MCU. How could it, there is no firmware on the
Octopus after all! I had to get a Micro SD, and followed the
[Klipper documentation to flash the MCU][klipper-flash]. Simple enough, `make` a
bit, then copy the compiled `klipper.bin` onto the SD, renaming it to
`firmware.bin`.

I’ll have to come up with a way to version the files. For now, I’m editing and
copying them between host and Voron manually.

[klipper-flash]: https://docs.vorondesign.com/build/software/octopus_klipper.html

Lo and behold, I have a dashboard! I did not dare push any buttons as to not use
any of the nonsense pins I entered, but we’re in software land now! Well, save
for all the wiring still to be done. The golem has arisen from the dead, while
it is still paralyzed, it is able to think and communicate.



Keeping track of time is becoming more and more complicated. I’m adding 1h for
setting up Mainsail OS on the Raspi (which I had done before the parts even
arrived).
  - Mechanical: 14h15m + 30m (Sexbolt) = 14h45m
  - Electronics: 5h45m + 2h30m (wiring, booting) = 8h15m
  - Software: 1h (MainsailOS)
  - Total: 20h + 4h = 24h

# 2022-11-03

Setting up temperature graphs in Mainsail for the Raspi and MCU temperatures was
simple, and took maybe 15min (software). Now I have some graphs!

Since I skipped bed installation (_way_) earlier, now is the time. The glue has
cured, and I can cut off the excess. I also cut gaps so I can screw the bed to
the rails. The first two are abominations, the second two are alright. I’ll keep
the PEI sheet on as much as I can so nobody notices. 30min mechanical.





Took a break (bouldering), then started a new session at 22:00. Cable chains time!

22:20 toolhead PCB mounted. Needed special part to hold it, but my friend got it
for me ahead of time, cool. (Why does Magicphoenix ship their own non-standard
PCB? Who knows.) Toolhead PCB: 20min. Has internal thermistor (for chamber
temperature measurement, which is a _terrible_ idea to measure so close to the
hotend), but that shares its slot with, well, the only thermistor slot, so that
one goes to the hotend one of course. Fans jumpered to 24V.



22:40 toolhead cable chain mounted, but it’s the thick one, meant for the
electronics-to-gantry part. Argh. Cannot use it because its minimum radius is
too big (and also because it’s needed for the Z axis).

23:00 X cable chain correct. It had just the right length: one element less and
X would be limited, one more and it would hit the window.

23:40. Y cable chain assembled. Left 3 elements out. Realized I forgot the
heater input for the toolhead. Fuck. Fiddle that through the X and Y chains.

1:15. Everything made its way down to the electronics compartment. Cable routing
is surprisingly unfun. I used very few zipties, slacking up the cables is
something I’ll do once wiring is finished at the bottom; the cables are long
enough anyway. Breakout PCB shoehorned onto one of the DIN rails, using a
leftover plastic part as spacer so the soldering tips don’t penetrate the
plastic it lies on. Added Z motor wires, and calling it a day. It’s a terrible,
terrible mess for later clean up.



Times:
  - Mechanical: 14h45m + 30m (bed) = 15h15m
  - Electronics: 8h15m + 3h15 (cable chains) = 11h30m
  - Software: 1h + 15m (temperature graphs) = 1h15m
  - Total: 24h + 4h = 28h

# 2022-11-04

## Session one: wiring (45m)

Broken window theory proves correct again, I’m making more of a mess because
there is a mess already.



Started machine: does not smoke. Connect to Mainsail. I see the heater
temperature!

## Session two: configuration out of home (2h)

Time for some configuration. Spent two hours giving the pins aliases. I did not
have the Voron available, so I configured the motors blindly with _lots_ of TODO
entries. Around 2h spent on software here.

## Session three: back home

### Wiring

My workplace is a terrible mess, the Voron’s wiring pales in comparison. I’m
starting to dislike having to literally jump over and losing other things. 15m
spent on cleanup, which was surprisingly quick to get back to a reasonable
level.

The next hour went into installing the Sexbolt (super quick) and the bed wiring
(not super quick since MagicPhoenix made the connector too big to pass through,
so I cut, crimped and wago’d it). I dread the wire cleanup. But config and
testing first! I also removed the circuits to bed in/out ports of the Octopus,
since the bed pulls its power from mains via the big relay, and that one can be
triggered using a normal heater output.

I thought about skipping LED wiring for now, but I’m glad I went for it, because
I was missing a cable! Where was it? Turns out I wired probe1 (meant for
inductive) instead of probe0 (Klicky). Klicky has two poles, inductive 3, so
that’s where my cable was hiding! Anyway, LED wired, Klicky wired.

### Stepper buzzing

Time to test the motors! Wiggle them using

```bash
STEPPER_BUZZ STEPPER=stepper_x  # moves towards front/right
STEPPER_BUZZ STEPPER=stepper_y  # moves towards back/right
STEPPER_BUZZ STEPPER=stepper_z
STEPPER_BUZZ STEPPER=stepper_z1 # needs inversion
STEPPER_BUZZ STEPPER=stepper_z2
STEPPER_BUZZ STEPPER=stepper_z3
STEPPER_BUZZ STEPPER=extruder   # E>0 moves up; not sure what direction is right
```

All motors move, but both steppers going towards the right when buzzing sounds
wrong. There’s [a helpful entry in the MagicPhoenix wiki][mpx-corexy-debug] to
help with that though. I can’t move the gantry without homing it first though.
Is there an override? Let’s worry about homing first.

[mpx-corexy-debug]: https://mpx.wiki/corexy_incorrect_xy_direction

### Homing switches

Klipper has a handy endstop test section in the machine config (why _there_?).
Manually triggered them and looked for a change in state. XYZ work, but Klicky
probe does not register.

Without homing, I can’t move; without moving, I can’t figure out what physical
direction the logical direction X corresponds to. But I _can_ set the homing
speed super slow and home! X goes in the right direction (right side), while Y
is inverted (towards front instead of back). The
[MagicPhoenix wiki][mpx-corexy-debug] says to flip motors in that case, which
was indeed the solution.



### LEDs

Configuring LEDs is pretty simple. Add the config section, use `SET_LED` to set
colors. Indexing starts at 1. Moved LED config to a sub-file, which is something
I’ll be doing with most config files in the future. Note: scp is garbage at
copying directories. It took me longer than a minute to do so correctly, so I
gave up (will downloading work, who knows, will it override my home dir, who
knows). Seriously, fuck the UX and manpages of _so many_ Linux tools.



### Fans

The fans worked right away. The part cooling fan can be controlled, the hotend
fan was tested by setting its threshold temperature to 10°C.

### Hotend heating

Bed and hotend were within a degree from each other, which I estimated is the
resolution of the thermal probes. Hotend fan worked. Time to heat it up, no? It
worked, but overshot the (conservative) target of 60°C by about 3°C. It’s
reassuring that the hotend cooling fan turned on immediately, and stayed on
until the temperature dropped below 50°C. Overshooting by 3°C isn’t that great
though at a test temperature of 60°C. I also heated to 100°C, 200°C and 260°C
(ABS printing temperature), it worked as expected. Once cooled down a bit I
think it’s time for PID calibration via
`PID_CALIBRATE HEATER=extruder TARGET=60`.

### Bed heating

Same procedure. 60°C first, works, with a single cracking noise; something
wasn’t set yet. I’m not too worried, because I did leave the screws of the bed
pretty loose, as per the instructions. Next, get some PID calibration for the
bed via `PID_CALIBRATE HEATER=heater_bed TARGET=60`.

While waiting for the results, I figured I might as well try out the extruder,
and indeed, as suspected in the buzzing test, it goes the wrong way. A simple
reversal of the direction pin should fix this.



### Chamber temperature sensor

Added sensor to config, reading looks okay, slightly above room temperature,
which makes sense after the bed heating test.

Times:
  - Mechanical: 15h15m + 15m (sexbolt, cleanup) = 15h30m
  - Electronics: 11h30m + 1h45m (bed, thermistors, sexbolt) = 13h15m
  - Software: 1h15m + 2h (config, blind) + 3h (config: buzz, homing, LEDs, fans,
    heating) = 6h15m
  - Total: 28h + 7h = 35h

# 2022-11-05

## Trello

I’m losing track of things to do, so I’ve created a Trello board to keep my
TODOs better than as a loose collection of comments here. Let’s see how that
goes. **Note from the future:** This was a good idea. So many things to do and
try.

## Sexbolt Re-reassembly (15m)

The bed of the MagicPhoenix kit is a bit higher than the normal bed, so the
Sexbolt was sitting too low for the nozzle to touch. Took it apart again
(distance to bed: 2.6mm), removed the Loctite residue with acetone (doesn’t work
that well, but worth a try) and reassembled it, but adding just a bit shy of
2.6mm to the screw by not fastening it to the end.

## Fixing the Klicky

The Klicky probe would not trigger during the previous end stop switch test. I
quickly debugged this by ~~being a genius~~ remembering my friend mentioning a
similar problem. And indeed, comparing the pinouts of the Octopus and breakout
PCB, it turns out the cable was flipped: GND went to signal and the other way
round! Seems like it’s a bug in the MacigPhoenix kit, and not a one-time fluke.
Using some very sharp pliers I undid the PCB plug and flipped polarity.

Tested it, and: it works! When attached, it triggers when pressed and does not
trigger when not. When not attached, it is set to triggered, so that failing to
pick it up for some reason does not start probing the bed without it.

## Configuring Z homing

Z homing has to be done by pushing the nozzle onto the Sexbolt, so the location
has to be precisely configured. But wait, I can’t do that because the travel on
the X/Y axes isn’t set correctly, so the Sexbolt position is not know so …

## Calibrating X/Y axes

This is a simple calculation,

rotation_distance = <full_steps_per_rotation = 200> * <microsteps = 32> / <steps_per_mm>
steps_per_mm = 200 steps/rotation * 1/20 rotations/tooth * 1/2 tooth/mm

## Z homing, for real now

Homed X and Y, started Z homing to move Z close to the bed, triggering the
Sexbolt when the nozzle was close to it. Then manually moved XY to (180, 257),
right above the Sexbolt. Homing works! I just have to be careful the wires still
hanging out of the toolhead don’t catch on anything. Zip ties are on the TODO
list.

## Adjusting Klicky height

I put in the Klicky holder without worrying about its height or alignment. This
requires some mechanical disassembly. Turns out it’s super easy! 5 minutes max.
Unscrewed Stealthburner (4 screws), took out hotend, adjusted Klicky holder to
be at the very bottom, put everything back together. I chose the very bottom
because it was already on that height on one screw, and it looked okay before,
just a bit slanted.

I also downloaded the [Klicky macros from the Github page][github-klicky-macros].

[github-klicky-macros]: https://github.com/jlas1/Klicky-Probe/tree/main/Klipper_macros



## LEDs misbehave

I noticed the LEDs sometimes show the wrong color, e.g. (R,G,B) = (1,0,0) yields
a teal LED. I don’t care about it enough to debug it right now, but it’s
something to fix later.

## Calibrate extruder, part 1

When ordered to extrude 10cm of filament, the extruder should do just that.
Apparently that’s often not the case, so I’ll start melting some first plastic!
Window is open because I have an un-enclosed un-nevermored cancer fume machine.
I’ve also tightened the nozzle, carefully, with a size 7 nut (and only a nut).

Now: unpack some ABS, and heat the hotend to 250 °C. Before doing this, I
noticed that it won’t let me extrude anymore because nozzle temperature is below
200°C, which I had previously configured. Nice! I then inserted some filament
(Esun black) with the clockwork open, pushed it all the way through, and got my
first extrusion.



Next step, calibration. I cut off the filament at 40mm above the Clockwork, and
told it to extrude 30mm. It extruded maybe one in this extrusion test #1. Come
to think of it, I should have done some config sanity checks before! Anyway,
22mm are still sticking out, so I extruded 40mm-22m=18mm, off by a factor of
30mm/18mm. I could now modify the config value by this factor but – wait, I have
this config value twice (33.500 and 22.6789511 a bit further down)! What’s the
setting Klipper actually uses in this case? Argh.

I’m keeping the value of 22.6789511, which the documentation says it’s a »good
starting point«. A very specific one, but okay. Alright, ew filament. Wait, how
do I change filament? Umm retract a bit, open Clockwork, and pull I guess. Works
well enough, although I’m a bit worried this might get some molten plastic onto
the extruder gears.

Extrusion test #2. This time, I put a little indicator (electrical tape) onto
the filament at 100mm. Ordered once again 30mm for extrusion, 18mm were
_actually_ extruded. I guess now I know that later values override previous one
in Klipper (at least in this case). The good news is that I can just apply the
factor 30/18 from above to the `rotation_distance`, which is then $22.6789511
\otimes \frac{18}{30}$. Wait, what’s $\otimes$? It’s the
I-don’t-know-whether-to-multiply-or-divide operator. Does 37.8 or 13.6 sound
like a more plausible result value? Underextrusion (18mm instead of 30mm) means
the rotation distance is too high, so the gears move less to extrude some
amount. 13.6(…) it is!

New attempt, extrude 30mm; marker went from 83mm to 53mm. Pretty good!



For some finer calibration, I’ll use up the rest of the test filament I’ve
inserted. While at it, I might as well use my caliper for some better
measurements. Moved filament marker way up. 177.33mm it says. Alright, extrude
150mm! Wait, skipped steps? Fuck fuck fuck. The heater has turned off in the
meantime, I extruded at slightly above 200°C so the safety didn’t kick in, but
extruding cooled the nozzle to 170°C. At least nothing broke! Alright, fiddling
with filament pieces is annoying, I’m getting the spool holder ready. For some
reason that one is part of Pif, even though it’s not super necessary to get
anything done (unlike e.g. the side panel fasteners, which are pretty much
_required_ for ABS printing).

## Spool holder (15m)

Simple enough, followed the instructions. I didn’t glue the PTFE tube into the
holder because it is bent in one direction from being spooled up, and that could
be used to have a tight mechanical fit.

## Calibrate extruder, part 2 (2h30m)

I cut ~10mm of PTFE tube open so I could clip it around the filament, which now
has its other end hidden deep into a big spool. This is my new extrusion marker.
Good idea, but unfortunately both hard to get onto the filament, and then it
doesn’t hold onto it very well, because completely unknown to me, PTFE is quite
slippery. Back to electrical tape it is.

Extrusion test #3. 192.81mm until marker, extrude 150mm at 5mm/s
(note: 10mm/s skips steps!). Marker is now at 45.52mm, so actual feed was
(192.81 - 45.52)mm = 147.29mm, underextrusion, `rotation_distance` is too high
by a factor of 150mm/147.29mm. Old `rotation_distance`) * 147.29/150 is the new
value, 13.36(…).

Extrusion test #4. 203.31mm until marker, extrude 150mm at 5mm/s. 52.91mm until
marker, 150.39mm extruded. We’re in sub-mm territory, good enough, but since we
already have the value, I might as well add another round of calculation. This
time it was an overextrusion, so the `rotation_distance` needs to increase by a
whopping 150.39/150. (We’re well below my measurement accuracy, and of course
the filament isn’t straight, but this is fun so I’m still doing it.)

Final value: `rotation_distance = 13.396270810234196`. Extruder calibration
done! Only took about 2h30m.

Times (it’s been a while, time for an inter-session summary):
  - Mechanical: 15h30m + 15m (Sexbolt boogaloo) + 15m (spool holder) = 16h
  - Electronics: 13h15m + 30m (Klicky) + 15m (fooling around) = 14h
  - Software: 6h15m + 1h (axes calibration, Z homing) + 2h30m (extruder config) = 9h45m
  - Total: 35h + 4h45m = 39h45

## Klicky probe: attaching, homing, docking

The next blocker on the way to the first print is the Klicky probe, for which I
have only ensured it triggers correctly.

First part, mechanical assembly. Super simple, two heat set inserts, T nuts into
extrusions, 15min, done.



Software is next. Surely I’ll need the Klicky location for that, so let’s figure
this out. Wait a second, the holder on the print head crashes into the
gantry-attached holder if I do that, the toolhead holder is too low. But even if
I fix that, doesn’t that mean part of the print bed is inaccessible, because
during a print the Klicky would be picked up?



I just worked on configuration for 2h, let’s see what I can still remember for
the build log. So, homing XYZ works, but is now done by the Klicky scripts,
which override the normal homing procedure to take into account that the probe
might still be attached. Other than that, they’re not that different.

The general idea is that the Klicky is outside of the printable area, around 1cm
besides the bed, so that it does not constrain the printable area. The location
of the probe is configured in the XY plane, and since it is attached to the
gantry, co-moving with and thus independent of Z. G28 (home all) drops the probe
if necessary, then does a usual homing cycle of X, Y, then Z. The `attach_probe`
picks up the probe coming from the front, and `dock_probe` moves it back into
its dock and gets rid of it by moving to the positive Y direction. This is my
test program:

```
G28
attach_probe
G01 X125 Y125 # Probing stuff goes here
dock_probe
```

Configuration wise, I’ve simply copied the `Klipper_macros/*.cfg` files of the
[Klicky repository][klicky-github] onto the printer. `klicky-variables.cfg` is
the configuration, the rest of the files don’t have to be touched for this step.
I heavily reduced all speeds for the probe for testing; however, the only
crucial setting is the `docklocation`, which much like the location of the
Sexbolt, I manually figured out by nudging the print head there.

[klicky-github]: https://github.com/jlas1/Klicky-Probe

## Quad Gantry Leveling (15m)

QGL probes the bed on its four corners, and adjusts the Z motors so the gantry
is parallel to the print bed. Configuration is simple enough, it pretty much
comes out of Klicky and setting the probing coordinates.

## Measure bed mesh

Now that the gantry is level, it’s time for having a look at the bed!



0.071mm variance. I don’t know whether that is very good, but it certainly isn’t
terrible considering it’s well below a typical layer height.

**Note from the future:** I should have written down how I did this. Simply
click the _Calibrate_ button in Klipper?

## Test print? Test print!

Some more configuration, write macro for starting/stopping prints that home,
QGL, all the things. 30min.

Since I’ll be printing ABS, I decided to attach the panels earlier rather than later.



And now let’s print the cube! Here are the first couple of layers:



lol, the Z offset is _off_. If the nozzle has the wrong height, at least I had
the non-damaging version of it!

After a few hours I found out multiple things.
- SuperSlicer allows setting a chamber temperature, Prusa does not. SuperSlicer
  it is from now on.
- The slicers generate Z moves with a feedrate of 18000, oh wow. No surprise
  movements are bonkers when the print starts. I set a maximum feedrate of
  40mm/s for the Z axis in the Klipper config, a 450-fold decrease.

And reprint. It’s a cube! Finally!





I can’t quite get a bearing in without hammering on it, but the exterior measurements are spot on.



The first layer was _terrible_ though, the Z offset was wrong, and I manually
had to add a bit to it. I used the textured sheet because I don’t like it much
and it’s a good spoil surface. I’m now printing a 3-layer high box just so I can
hopefully peel it off the print sheet and get the otherwise irremovable residue
of the cube’s skirt off.



Times are hard, I lost track of time, but I think including breaks I spent
around 12h (wat) on the printer today, all of it on configuration.

  - Mechanical: 16h + 15m (Klicky) = 16h15m
  - Electronics: 14h
  - Software: 9h45m + 2h (Klicky) + 15m (QGL) + 15m (bed mesh) + 30m (macros) +
    (oh boy I lost track of time but total has to be 12h today) 4h = 16h45m
  - Total: 39h45 + 7h15m = 47h

# 2022-11-06

## Foam pads for side panels (1h)

It took me 45m to glue the foam strips onto the panels for the back, top, and
two sides. I postponed it because I thought it wasn’t super necessary for the
initial prints, and because it would not be fun. I think I was wrong on both
accounts: chamber temperatures over 40°C were super hard to attain
(41-dot-something degrees after the 1h calibration cube prine!), and also it
actually was fun to attach them accurately! I should have done this much
earlier.

I also did the whole Loctite trick for the couple of panel holders my friend got
me for cheap removable panels: secure them with M3 hammer nuts with Loctite, but
fasten them just so you barely feel resistance. Wait for the Loctite to cure and
you’ve got yourself hex-nut somewhat-quick removable panel holders.

In total, this is 1h mechanical assembly today.

## Involuntary first layer art

The rest of the time I spent on trying to print some smaller addons, but I’m
having serious trouble with bed adhesion, and the first layer is also 0.05mm too
low so that I can hear the nozzle scratch over the surface if I don’t calibrate
it quickly enough. Bed is at 110°C, chamber at 44°C, still I’m getting results
like this test piece (single .2mm layer rectangle):



Before I can fix this issue, there’s no way I can print e.g. the Nevermore.
**Note from the future:** The Klicky mount on the toolhead was at an angle, so
the Klicky wasn’t parallel to the bed. This resulted in a wrong effective switch
height, and messed up the Z calibration. The fix was done on 2022-11-07, but is
only briefly mentioned in the buildlog.

Times:
  - Mechanical: 16h15m + 1h (panels) = 17h15m
  - Electronics: 14h
  - Software: 16h45m
  - Total: 47h + 1h = 48h

# 2022-11-07

What got my print quality from begging for the first layer not to detach and
then seeing it detach, to decent quality:

1. Clean the print sheet with soap, rinse, then clean with IPA. I think this one
   was the most important.
2. Fixing the Klicky so that the first layer is okay. The switch is now parallel
   to the print bed when attached. I now have printed-part-visible scratches on
   the smooth PEI sheet from when it wasn’t level. Oh well, it’s now my spoil
   board. **Note from the future:** Tried getting a replacement sheet, out of
   stock everywhere. Restocking will take at least a month. Argh.
3. Extrusion factor 90% for ABS.

I printed the blind cover for the exhaust hole with tolerable quality, the fan
casing and lid of the Nevermore with terrible-but-workable quality, and after
these changes the next part was pretty good.

Times:
  - Mechanical: 17h15m + 45m (Klicky levelling, clean PEI sheet) = 18h
  - Electronics: 14h
  - Software: 16h45m + 15m (extrusion factor and research) = 17h
  - Total: 48h + 1h = 49h

# 2022-11-08

## Fixing mysterious motor outage (30m)

Everything was fine yesterday, I showed the printer to someone, movement was
fine. The next day, stepper A (right) would only vibrate, not move. What!

- Measured cable: all wires OK.
- Measured stepper: OK. Red/blue connect, green/black too.
- Switched motor slot. A was on #0, same behavior on #7 though.
- Switched drivers (TMC2209) on slots #0 (A motor) and #1 (B motor).
  Expectation: B misbehaves instead of A. Result: both behave. Umm what? Okay,
  cool that it’s fixed, but I have learned _nothing_.

## Cover exhaust slot (15m)

While at it I also put in the cover for the exhaust slot, replacing my not very
sturdy cardboard-and-adhesive-tape construction.



## 24V relay (1h45m)

In case of an emergency exit or Klipper otherwise messing up, I want power to be
taken away from the Octopus. This will stop heating, printing, everything. For
this, I bought a relay, which was helpfully labelled in Chinese and had screw
terminals so hard if you can open them you’ll be crowned king of England.
Anyway, I wired it in, gating the AC input to the 24V PSU. Wiring is easy when
you’re shameless, so here’s how that looks now:



An explanation is in order!

### Raspi part

The three wires (Vcc, GND, signal) are connected to 5V, GND and the Raspi’s
GPIO17. I then made the Raspi an MCU by running what the
[Klipper docs on that topic][klipper-raspi-mcu] tell me:

```bash
sudo cp ~/scripts/klipper-mcu-start.sh /etc/init.d/klipper_mcu
sudo update-rc.d klipper_mcu defaults

cd ~/klipper/
make menuconfig

sudo service klipper stop
make flash
sudo service klipper start
```

[klipper-raspi-mcu]: https://www.klipper3d.org/RPi_microcontroller.html

### Configuration part

```ini
# moonraker.conf
[power main_24V_power]
type: gpio
pin: !gpiochip0/gpio17
off_when_shutdown: True # Shut down 24V and bed on Klipper shutdown (!)
initial_state: off
```

### Relay part

The wires from the Raspi are simply connected to their counterpart pins. The
jumper controls whether the relay shares its own Vcc with the Raspi; since I
don’t want to add yet another wire, I’ve let it in. Apparently this can be a
problem should the relay do something crazy or whatever, but I don’t think
that’s relevant for my simple circuit (because of optimism ignorance, I’m no
electrical engineer).

As mentioned, the screws on the relay were reasonable (normally open),
unreasonable (common) and ridiculously I-am-killing-the-screw-when-turning-it
stupidly hard to turn. I don’t know much about relays so I booted the Raspi
without the AC connected to the relay and measured where the connection was.
Without power, there was no connection between center and left (normally open,
misleading name or what?!). The other side was the inverse. I even pulled the
Vcc cable from the activated relay to check whether loss of Raspi power closes
it. Anyway, the wiring is a bit hard to see in the picture, but the relay is
closed by default, I have to manually enable it in the menu once it is shut
down, and I never have to shut down my Raspi anymore. Clicking the button
audibly toggles the relay, and soon enough the LEDs on the Stealthburner light
up.



I spent a total 1h45m on this.

Times:
  - Mechanical: 18h + 15m (exhaust slot) = 18h15m
  - Electronics: 14h + 30m (fixing motors) + 1h45m (24V relay) = 16h15m
  - Software: 17h
  - Total: 49h + 2h30m = 51h30m

# 2022-11-09

## Pressure advance

I followed
[Andrew Ellis’ guide to tune pressure advance][ellis-pressure-advance], and
chose the parameters according to my still somewhat slow configuration,

  - eSun ABS+ black
  - Slow printing speed: 300 mm/min
  - Fast printing speed: 7200 mm/min
  - Printing acceleration: 2000 mm/s²

The code runs for a bit over 5min. The numbers are unreadable, but comparing it
with the Mainsail preview of the GCode I counted the lines, and settled for
0.05s.

[ellis-pressure-advance]: https://github.com/AndrewEllis93/Print-Tuning-Guide/blob/main/articles/pressure_advance.md



# 2022-11-10

I did everything pretty much in one go, for a 2h30m session. Pretty much all of
it was mechanical (plugged in two fan cables), and some parameter tuning.

# Decontaminator (2h)

The decontaminator is a little brush with a bucket next to it. The idea is to
extrude some filament, wipe the nozzle on the brush, and have a clean start
without ooze guaranteed before every print. Installation is simple enough. It
even comes with slots for magnets so it snaps into place, if only my screws were
magnetic (Note from the future: they’re M3x8 ones). Another benefit I can’t use
is that it allows tiny screws to stick out ontop that act as a PEI sheet
stopper, but my screws are too short, so I’m not having any of that. The brush
is where the Klicky used to be, which I relocated with a special side mount. The
nozzle can just barely touch the brush so the layout is fine for now. I did not
configure the firmware to use the decontaminator yet though, so this will have
to wait until later.



# Electronics fans (εm)

I installed fans for the electronics compartment. After an initial test of
having them PID controlled and failing to keep them to low, non-oscillating
levels, I decided to revert to the old temperature measurements, and having them
as manually controlled fans in the firmware. PID is something I can worry about
in the future.



Oops, I just noticed the purge bucket collides with the Klicky when homing Z. A
problem for another day, for now I’m simly removing the bucket.

Times:
  - Mechanical: 18h15m + 2h (screwing, unmounting, mounting, glueing) = 20h15m
  - Electronics: 16h15m + ε (fan plugs) = 16h15m
  - Software: 17h + 30m = 17h30m
  - Total: 51h30m + 2h30m = 54h

# 2022-11-13

## Nevermore activated charcoal chamber filter (45m)

I finally put in the Nevermore, an activated charcoal filter to get rid of that
cancerous styrene ABS produces when heated. I’ve had to reprint the charcoal
compartment, because embarassingly enough I glued the magnets in repellant
direction.

Since I had to take the bed out to install it, I also took the opportunity to
route the bed cables through the hole in the base plate (it was previously going
through the drag chain hole).



The filter wouldn’t start on the first attempt because the cable had the wrong
polarity; the removal of the cables from the JST plug again was a bit difficult,
but I managed to flip them, and the fans started working. It’s super nice to be
able to shut off the relay for the 24V circuit, I could do this whole thing
while the Raspi was powered.

## Purge bucket hacking and slashing (15m)

In the last session, I remarked that the Klicky hits the purge bucket. I used
side cutters to get rid of some of the bucket, and the layer lines allowed me to
cleanly pry off the rest of the bucket so that it is less high on one side. This
fixes the Klicky issue, without having to do any CAD modding. I also put some
Acetone onto the wound to make it heal better. Get well soon, purge bucket.



Times:
  - Mechanical: 20h15m + 45m (Nevermore) + 15m (purge bucket) = 21h15m
  - Electronics: 16h15m + 15m (Nevermore) = 16h30m
  - Software: 17h30m
  - Total: 54h + 1h15m = 55h15m

# 2022-11-15

## Enabling exclude object (15m)

This is not something I did today, but since I used it yesterday during a
partially failed print, here’s how Klipper’s Exclude Object functionality works.



Simply click on the part you want to stop (first layer issues, not needed
anymore, etc.) and it will be ignored during the remainder of the print.

Enabling this is quite easy:

1. In the slicer (SuperSlicer, in my case), enable _Label objects_ in _Print
   settings → Output options_.
2. In `moonraker.conf` add
   ```ini
   [file_manager]
   enable_object_processing: True
   ```
3. In `printer.cfg`, add `[exclude_object]` (argument-less section). Forgetting
   to do this creates lots of (harmless) `Unknown command: EXCLUDE_OBJECT_START`
   errors during printing.

That’s it.

## Flow rate measurements (2h)

I spent roughly 2h on handwriting GCode (macros) for nozzle flow rate testing.
The idea is to extrude a certain length of filament at some volumetric flow
rate, to determine the limit of the hotend/nozzle combo.

Some emergency restarts were required when the nozzle didn’t lift enough, and
became a pea-sized blob of goo. Nothing bad happened, but now the relay is
broken (permanently on). It might also be the GPIO pin on the Raspi. Strange,
because from its point of view an emergency shutdown is nothing special: send
GCode, flip GPIO output pin. Luckily, I have a spare relay that I can use.

Times:
  - Mechanical: 21h15m
  - Electronics: 16h30m
  - Software: 17h30m + 15m (exclude object) + 2h (gcode) = 19h45m
  - Total: 55h15m + 2h15m = 57h30m

# 2022-11-17

## Replacement relay (15m)

It looks like the relay was the broken part, not the GPIO parts.

# 2022-11-19

## Display installation (30m)

Today I mounted the display, and also put the breakout PCB onto a DIN clamp that
did not involve a ziptie. The config I simply copied from a friend, which didn’t
really cost me any time.



## Rewiring (1h30m)

Next stop was something I had postponed _many_ times, cleaning up the wiring.



The motors are the closest to the bed, one layer above are the sensors and the
breakout PCB cables. It wasn’t terrible to do, but I would lie if I said it was
a lot of fun. Still, it looks much cleaner already.



I haven’t touched the AC/DC wiring much, that will have to wait until another
time.

Oh, and the relay did not allow me to turn off the Octopus earlier. Looks like a
systematic problem to me! Maybe I should remove it in case it starts acting up
during printing?

## Resonance compensation

### Wiring (1h15m)

I spent 1h15m looking for a cable, crimping female connectors on one end (I’m a
slow crimper), putting the pins onto the Raspi and double-checking the wiring
mechanically (can’t buy a new one if I fry it). I followed
[the guide in the Klipper docs][klipper-measuring-resonances] and verified the
Raspi pinout with another website.



[klipper-measuring-resonances]: https://www.klipper3d.org/Measuring_Resonances.html

Cool, let’s go. No smoke when starting the Raspi, excellent.

### Measuring (1h)

This is pretty straightforward. The documentation is a bit spread out in the
Klipper docs between the config docs and the measurement section, but it’s not
too hard to put them together.

```ini
[adxl345]
# Yes, None, not the Raspi pin CS is connected to (GPIO08/SPI0_CE0_N in my case).
cs_pin: raspi:None

[resonance_tester]
accel_chip: adxl345
axes_map: y, z, x # Because of my mounting: printer(x,y,z) = sensor(y,z,x)
probe_points:
    125, 125, 25 # Bed center, Z in safe height
accel_per_hz: 25
  # ^ Default is 75, but start with lower
  # accelerations to check out how loud it is
hz_per_sec: 2
  # ^ Default is 1, but 2 takes less time at the
  # cost of precision. Just right for testing
  # the setup before the measurement.
```

Upload the config, accelerometer, what do you say?

```
> ACCELEROMETER_QUERY
accelerometer values (x, y, z): -296.082377, 4367.215058, 9729.412825
```

Okay that’s three values and not an error, I guess that’s not bad. Resonance
measurement time!

```
TEST_RESONANCES AXIS=X
```

The print head is audibly-but-not-visually vibrating. Less than an electric
toothbrush. Alright, increase `accel_per_hz` to `50`. Approaching the electric
toothbrush. `75`, Klipper’s default value. Like an electric toothbrush but with
more mass. Almost, but not quite yet, worried about my neighbours (it’s 2
o’clock). Okay, time for the real run: first x then y, with `hz_per_sec: 1`.

Run the analysis tool,

```bash
for file in /tmp/resonances_{x,y}_*.csv; do
    ~/klipper/scripts/calibrate_shaper.py "$file" -o "$file.png"
done
```

And here’s the output with some nice recommendations:

```
Fitted shaper 'zv' frequency = 50.6 Hz (vibrations = 4.5%, smoothing ~= 0.066)
To avoid too much smoothing with 'zv', suggested max_accel <= 10000 mm/sec^2
Fitted shaper 'mzv' frequency = 48.8 Hz (vibrations = 0.0%, smoothing ~= 0.086)
To avoid too much smoothing with 'mzv', suggested max_accel <= 7000 mm/sec^2
Fitted shaper 'ei' frequency = 58.6 Hz (vibrations = 0.0%, smoothing ~= 0.094)
To avoid too much smoothing with 'ei', suggested max_accel <= 6400 mm/sec^2
Fitted shaper '2hump_ei' frequency = 73.2 Hz (vibrations = 0.0%, smoothing ~= 0.101)
To avoid too much smoothing with '2hump_ei', suggested max_accel <= 6000 mm/sec^2
Fitted shaper '3hump_ei' frequency = 88.2 Hz (vibrations = 0.0%, smoothing ~= 0.105)
To avoid too much smoothing with '3hump_ei', suggested max_accel <= 5700 mm/sec^2
Recommended shaper is mzv @ 48.8 Hz
```



```
Fitted shaper 'zv' frequency = 40.8 Hz (vibrations = 30.4%, smoothing ~= 0.097)
To avoid too much smoothing with 'zv', suggested max_accel <= 6500 mm/sec^2
Fitted shaper 'mzv' frequency = 37.0 Hz (vibrations = 10.0%, smoothing ~= 0.149)
To avoid too much smoothing with 'mzv', suggested max_accel <= 4000 mm/sec^2
Fitted shaper 'ei' frequency = 33.8 Hz (vibrations = 10.7%, smoothing ~= 0.282)
To avoid too much smoothing with 'ei', suggested max_accel <= 2100 mm/sec^2
Fitted shaper '2hump_ei' frequency = 48.6 Hz (vibrations = 2.5%, smoothing ~= 0.228)
To avoid too much smoothing with '2hump_ei', suggested max_accel <= 2600 mm/sec^2
Fitted shaper '3hump_ei' frequency = 48.0 Hz (vibrations = 0.1%, smoothing ~= 0.356)
To avoid too much smoothing with '3hump_ei', suggested max_accel <= 1500 mm/sec^2
Recommended shaper is 2hump_ei @ 48.6 Hz
```



The physicist in me is fastinated with the fact that the two axes have different
algorithm recommendations, most likely because the y axis has a lot more mass to
move, but the human in me who needs to go to bed simply copies the
recommendations to the config.

```ini
[input_shaper]
shaper_freq_x: 48.8
shaper_type_x: mzv
shaper_freq_y: 48.6
shaper_type_y: 2hump_ei
```

Times:
  - Mechanical: 21h15m + 30m (screen, PCB mount) = 21h45m
  - Electronics: 16h30m + 1h30m (rewiring) + 15m (relay replacement) + 1h15m (accelerometer) = 19h30m
  - Software: 19h45m + εm (screen config) + 1h (resonance measurements) = 20h45m
  - Total: 57h30m + 4h30m = 62h

# 2022-11-20 Speed tuning

2h speed tuning using [Andrew Ellis’ macro][andrew-ellis-speed-macro]. Settled
for 10k mm/s² acceleration and 500 mm/s speed. 700 mm/s speed skips steps (and
bangs the gantry against itself), 12k mm/s² works without errors so 10k is a
safe value. All tests were run with the printer cold, so some generous safety
margins are in order.

[andrew-ellis-speed-macro]: https://github.com/AndrewEllis93/Print-Tuning-Guide/blob/22ed63d984c43e63ba6dfdd223ffaa40d82aa779/macros/TEST_SPEED.cfg

I then entered these values in my slicer as machine limits, and tried to get a
Benchie to slice to less than 30m. I didn’t quite manage to do it, but
`Print settings | Speed` is where it’s at. Accelerations in particular play a
big role in the estimated printing time. I pushed them hard-but-not-too hard,
and got a 38m Benchie according to the slicer. Most time is spent on the
perimeters, the settings for those in the end were:

### Speed

- Default speed: 200 mm/s
- Perimeter speed: Internal 100% (of default), external 50% (of internal)
- Infill speed: Solid 120%, Sparse 100% (of solid, so 120% default), top solid
  50% (of solid, so 60% of default).

### Acceleration

- Default acceleration: 8000 mm/s²
- Internal perimeters: 100%
- First Layer: 2000 mm/s
- Rest all set to 0

Times:
  - Mechanical: 21h45m
  - Electronics: 19h30m
  - Software: 20h45m + 2h = 22h45m
  - Total: 62h + 2h = 64h

# 2022-11-{23,24}

## No more adhesion problems (15m)

My bed had two issues: a) I violated it multiple times by audibly scratching the
nozzle over it because of bad Z calibration, leading to very visible markings
all over the place; b) low adhesion, sometimes even with brim on big parts. My
brother recommended to sand the PEI sheet with fine sandpaper. Bought some
P1200, sanded it down, printed a Voron test cube (24m, limited by flowrate of
15mm/s), and holy shit adhesion is reminding me of PETG. It’s almost too good,
or maybe _actually_ to good. Time to disable brims in the slicer again!

## Flow rate tests revisited

Spent way too much time on this to record it here trying to optimize printing
the test pieces in bulk. But turns out the nozzle likes to keep plastic stuck to
it if you don’t smear it on the print bed, so something always caught and moved
around. In the end I just did single extrusions of 200mm at various feedrates,
and used my mg scale to measure their masses. I’m not sure how precise that
cheapo scale is actually, but here’s the data as read from it with the standard
Phaetus 0.4mm nozzle:

| Flow [mm³/s] | Mass [mg] | Comment |
| ---:| ---:| --- |
| 10.0 | 514 |
| 11.0 | 518 |
| 12.0 | 512 |
| 13.0 | 512 |
| 14.0 | 513 |
| 15.0 | 516 |
| 16.0 | 504 |
| 17.0 | 508 |
| 18.0 | 502 |
| 19.0 | 502 |
| 19.5 | 493,486,494,492,495 | Skipping
| 20.0 | 473 | Skipping

Interestingly enough, the drop is pretty small, and happens around the 15mm³/s
mark. I think this is a safe setting for further printing with the standard
nozzle.

Nozzle change, Bondtech CHT 0.4mm. Using some uncalibrated test extrusions I
figured out skipping happens around 25mm³/s, so I’ll space my measurements out a
bit.

| Flow [mm³/s] | Mass [mg] | Comment |
| ---:| ---:| --- |
| 10.0 | 510 |
| 12.0 | 512 |
| 14.0 | 521 |
| 16.0 | 513 |
| 18.0 | 513 |
| 19.0 | 506 |
| 20.0 | 497 |
| 21.0 | 510 |
| 22.0 | 506 |
| 23.0 | 514 |
| 24.0 | 510 |
| 25.0 | 506 |
| 26.0 | 494 | Skipping

This is the data as simple plot,

```mathematica
phaetus = {{10.0, 514}, {11.0, 518}, …}
cht = {{10.0, 510}, {12.0, 512}, …}
ListPlot[
    {phaetus, cht},
    AxesOrigin -> {10, 450},
    AxesLabel -> {"Flowrate [mm³/s]", "Mass [mg]"},
    PlotLegends -> Placed[{"Phaetus", "Bondtech CHT"}, Below]
]
```



What do I see?

- My scale is probably not the best. Cheap one from Amazon.
- No dramatic falloff before skipping starts. Maybe if my extruder tension was
  higher, I could push some harder plastic through the nozzle still?
- Bondtech CHT has much higher flow limits
- Statistics here are really bad, but data is good enough so I can increase my
  flow rate limit in the slicer to 20mm³/s with the CHT nozzle

# 2022-11-25

## No more time keeping

The printer is now reasonably well-working, I’ve applied for a serial number a
week ago (but haven’t received it yet), and I consider the build done. This
being a hobby project it won’t be finished anytime soon, but I’ve decided it’s
not a good idea to keep a total time anymore. I’ll annotate headlines with time
spent if applicable, but the times section is gone from now on.

## Sanded PEI sheet texture

The sanded PEI sheet is gicing me problems. Adhesion is very strong, but the
surface finish is sometimes a bit off-black, maybe because of stretching when
pulling it off? Also previous prints leave their mark, so maybe this is a bit of
a high-maintenance mod if I have to re-sand it frequently.

## First layer calibration

I printed a 1-layer box to check my first layer, and also to clean it as a side
effect. I noticed some interference patterns, indicating a nozzle too close to
the bed. Indeed, adjusting the Z offset by 0.1mm (to a total of +0.8mm) solved
the issue and gave me a very nice first layer. It seems like there’s still an
issue with my Z calibration script.



On the other hand, holding the layer against the light shows some gaps,
indicating not being close enough to the bed. I should do a new bed mesh!



# 2022-11-26 Cleanup day (4h)

Today I did some of the tasks I postponed for way too long. None of these were
strictly necessary, but I decided to spend some time getting them off my
concience. Most importantly, the printer looks finished now.



## Chamber cable management

I didn’t exactly go overboard with zipties on the build, and some cables were
routed when the zip ties were already in place. The Y-to-X transition on the
gantry now doesn’t have any loose ends anymore, the chamber thermistor is now on
the cable chain guide and properly routed (it was just inside the cable chain
before), and the back-left motor has its cables tucked in the gantry extrusion
using [these](https://www.thingiverse.com/thing:2246832) clips.



**Note from the future:** The back of the zip tie in the above picture rubs
against the gantry belts and is _terrible_ placement. Once I figured this out
(2022-12-03) I saw some abrasion on the back plate, and cut it off during a
print to avoid any further damage to the belts.



A note on the thermistor, the cable was too short to route it along the rest of
the breakout-to-gantry cables. Avoiding the detour by threading it through the
bed hole gave me enough slack, so that’s why there’s a black cable going from
beneath the bed to the Z drag chain. You can see this in the picture of the PEI endstop nails in the next section.



## PEI endstops

The purge bucket mod has holes in its parts to put screws in that serve as an
endstop for the PEI sheet, so that I don’t have to carefully put it in straight
and avoiding the Sexbolt and nozzle brushes.



## Other

I also did some wiring cleanup in the electronics compartment and installed the
frontal skirts. The next print will be the back and left side skirts.

# 2022-11-27

## Ground your frame, dumbass

**Note to the past.** The 24Vcc wire loosened when doing the wiring and settled
against the frame when I reassembled it. Nothing happened, but had it grounded
itself through me that wouldn’t have been a lot of fun, neither for me nor for
the electronics.

## Manual fans again

Enabled manual fans for the electronics compartment again, for two main reasons:

1. The motor drivers don’t have their temperature monitored. They should get
   some constant cooling though. Basing the Octopus-facing fan on its MCU
   temperature simply uses the wrong temperature measurement.
2. It’s annoying to have the fans go on and off, much more so than them running
   at a constant 25% or so.

# 2022-{11-28 .. 12-03}

## Adhesive tape based hinges (1h)

There are some pretty cool hinges around that are removable and use magnetic
joints instead of screws, making them easily removable. Unfortunately the tape
doesn’t seem to work well with my full frontal door, the design is probably only
suitable for two half doors with much less mass and leverage. I’ve removed the
hinges again, and will probably use some with drilled holes for added stability
in the future. For now, it’s back to using panel clamps for the door.



## LED strips for chamber illumination (3h)

I got these 10W/m LED strips from a friend, who had them left over from their
Voron. They are only white but pretty bright. I cut them into four 350mm strips
and [printed some rails][voronmods-franz] so they fit into the extrusions
nicely. I’ll also put nail polish onto the intermediate contacts so there’s an
additional layer of isolation between them and the extrusion (in addition to
physical distance and the coating, but I feel nail polish is very simple and the
only part that’s fully under my control).

[voronmods-franz]: https://github.com/fmthoma/voron-mods



After soldering them together – ideally using crossing wires so they bend nicer
around corners, which I forgot for the first connection – they look like this
when tested on a heater port:



This is 1% brightness. 10% is uncomfortable to look at, and 100% is stupidly
bright. Sure, the panels eat some of the light, but I think 10% will be _plenty_
of light for normal operation.

Right now, they’re hanging out to dry, which gives me some time to write this.
o:-) Meanwhile I have to prepare mentally for undoing some of the very first
screws I added: the LEDs require removing the top square of the frame for
assembly. Loosen Z belts, take frame apart, insert LEDs, carefully reassemble
frame, easy (I hope, bit stressed about this to be honest).



It wasn’t so hard it turns out! I just wish I had made my wires (50mm) a bit
longer. They are pretty much exactly long enough when in place, but a bit
annoying to install. The whole process was a bit awkward, but didn’t take too
long and was also a nice fun throwback to working on the frame a month and some
80-very-ish project hours ago.

And now, fiat lux!



The LEDs actually flicker quite a bit when the heater is running, because they
are driven by the 3rd heater’s PWM slot. Increasing the PWM frequency from
Klipper’s standard of 10Hz to 100Hz solves the issue though.

Afterwards I had some problems with the part cooling fan, it would not turn
well, and only wobble a bit during kickstart. I played with the parameters a bit
and at some point the problem resolved, and the fan worked even with the old
parameters. The problem seems to be solved, but I’ll have to keep an eye open
for something like this happening during a print!

# 2022-12-05 Extrusion multiplyer tuning

I’ve never really tuned my extrusion multiplier, so I used
[Andrew Ellis’ instructions][ellis-em-tuning] for doing so. A friend told me
this is a good idea to do per filament brand; the red one in the picture is from
Polymaker, so far I’ve also used eSun a lot. The result isn’t very conclusive
though, I’ll keep my 0.94 multiplier. 0.92 has better surface smoothness but
worse perimeter adhesion; the difference isn’t that big to worry about though.



[ellis-em-tuning]: https://ellis3dp.com/Print-Tuning-Guide/articles/extrusion_multiplier.html

# 2022-12-06

Sometimes when doing Z lifts of 5cm or so, I heard something like a skip. I
couldn’t make out the location and the prints were fine. Until they weren’t and
I had a proper ugly layer. Turns out the back right Z belt from the motor to the
big gear wheel was very loose! I re-tightened those loops by loosening the motor
and foot screws, realigning them, and fastening them with proper tension. Now
all the short Z loops make an audible sound when plucked again. Especially the
offending belt was quite wobbly before.

This also explains why I had trouble with the nozzle being too close on prints
on the back right: the motor would simply lose a couple of steps until the
gantry is kind of carried by the remaining three motors only!



The Part cooling fan is still giving me trouble; I was hoping for a bad contact
in the Stealthburner PCB and re-plugged the plug, but that didn’t change its
behavior. It still sometimes goes on and off without good cause.

# 20222-12-07

In today’s episode of convenience mods that I should have added much earlier:
I’ve installed front door hinges. No longer do I have to take the front off in
order to access the internals. Installation was done by having the door attached
as before, adding the hinges, temporarily securing them with adhesive tape, and
then drilling the holes in the right spots halfway through. Then I took off the
taped hinges, finished the holes, and attached the screw counter plates. Socket
head screws were unfortunately too big and collided with the belt tensioning
units that move up and down with the gantry, so I had to opt for flat head
screws. The kit only comes with M3x6 which are too short, I bought M3x8 which
work, but I think the best fit would have been M3x10. The door is well-secured
though, so I don’t think I’ll ever have to change the screws.



# 20222-12-{20,21} Tap

The PCB and parts kit arrived, let’s build this!

## Assembly outside of the printer (1h)



Like all good things, it starts with heat set inserts, then following the
manual. As usual, it gives instructions, but doesn’t justify them. For example,
why leave those 2.5mm gap on two of the screws? Well, it’s where the hotend
module attaches to, but it won’t tell you that.

The PCB I ordered had the connector’s pins stand out a bit too much on the back,
so I had to cut them off to make the back of the PCB pretty much flush. Holes
and screws were decently sized, the magnets are a nice press fit (with an
additional drop of glue).

Unfortunately, the Tap can’t be fully assembled and then inserted: since the
linear rail carriage covers the screws that attach the print head to the X
carriage, it has to be installed before fully assembling the unit.



## Assembly inside of the printer (45m)

Taking things apart that haven’t been taken apart for a while is always a bit of
an uneasy nostalgia.



Threading the belts is a bit finnicky, but at least there’s enough slack in the
tightening screws so that it’s not too bad. I didn’t detach the toolhead fully,
giving me less room to work, but I think this was the better choice. Removing
the Klicky JST connector was surprisingly hard, because the PCB is very tight.

Anyway, mechanical assembly is done, I now have a red element in my printer
that’s not that easy to remove so I kind of _have_ to switch to my red/blue
color scheme at some point.

## Electronics (2h15m)

The Klicky connector had two wires, the optical sensor has three, so I cannot
just swap cables and be done with it. Crimping little Plugs is not a friend of
mine (or my tools?). I estimated the wire length using an old piece of filament
as tester, it came out at 95mm. I forgot taking a picture of the PCB’s pinout,
but luckily it’s printed on it so it can be seen when lifting the tap a bit,
lucky me!

Pinouts:

  - Sensor PCB, top to bottom: Vcc, signal, GND. Bump pointing to the printer’s
    back.
  - MagicPhoenix toolhead PCB: VCC, signal, GND. Bump pointing to the printer’s
    front.

So the cable has to be crimped just parallel, with both bumps looking up on the
table.

My crimping pliers are _shit_, I think they’re made for much bigger connectors.
Anyway, I can’t get the crims right, so my fallback is a makeshift crimp using
normal pliers, and then soldering the connectors on. 1h15m spent on crimping,
recrimping, soldering, blocking the crimps with soldering tin.

Another hour on electronics the next day. Since the new probe is a 3-wire one,
the old probe cable from the Octopus to the breakout PCB didn’t work anymore,
since it now needs to connect to PROBE1 (formerly PROBE0). Since the power
supply is by the breakout PCB anyway, I simply created a short adapter.



Booted it up, everything works! There’s even an LED on the PCB that indicates
whether the trigger is active; it lights up red when the optical sensor is
triggered (which it is, by default).



No worries about the broken bottom of the Stealthburner front though, that was a
little accident a few days ago (had stuff in the chamber while homing), and is
unrelated to Tap.

## Configuration (1h)

Software-wise the configuration is alright, Klipper doesn’t allow using the same
pin twice, so Z homing gets the special virtual pin `probe:z_virtual_endstop`.
First tests were with a catron tube that once held my toilet paper (cheaper to
crash into that one than the bed), but all tests ran smoothly, and I quickly
went to live Z homing and QGL.

Calibrating the Z switch offset is maybe the most important step. With a probe
offset of zero, Z homed, and a flashlight behind the nozzle, I found the Z value
when the nozzle seems to start touching the bed: between 0.8 and 0.9mm. I then
tried to fine-tune it using a feeler gauge, and I could push the 0.03mm one
under the nozzle starting around 0.88mm Z position. This matches my flashlight
estimation of 0.85mm, so that’s the value I’m using as my probe offset: `-0.85`,
because the probe triggers when it’s below the bed (tap raised).

With everything in place, time for a `PROBE_ACCURACY samples=100`! The results
are quite impressive:

- maximum -0.841250
- minimum -0.853750
- range 0.012500
- average -0.848713
- median -0.848750
- standard deviation 0.002684

## Macro fine-tuning (30min)

Tap works, but now it needs to be incorporated into the printing macros! In
particular, I don’t want a 260°C nozzle directly on my bed. The solution is to
add some logic to the `activate_gcode` part of the `[probe]` section that makes
sure the temperatures are right.

## Fallout

I reduced the probing sample size to one thanks to the Tap’s accuracy, making
QGL and bed meshing much quicker. The bed mesh shows a funny feature: the back
left is wonky! It looks like the nozzle brush is actually interfering with the
hotend. Investigating the config showed that there was still an offset for the
Klicky built in. Removed the offsets so that the bed is now probed at (5,5) to
(245,245).

## Finetuning probe offset

The probe offset can be measured, but I don’t want accurately measured first
layers, I want well printed first layers. I sliced a one layer high square and
printed it with various Z offsets. +0.10mm yielded a very gappy first layer,
+0.05mm had too much plastic for the height, +0.06mm was just right. The new
offset is thus `-0.85 + 0.06 = -0.79`.

Turns out this value was a bit off, and once again following Andrew Ellis’ print
guide I settled on an experimentally determined value of `-0.945`. I simply
sliced a 25mm×25mm×0.2mm cuboid and printed 9 of them in a square pattern, and
modified the Z offset when the printer switched to the next one using direct
display controls (which set values in Klipper directly and don’t have to wait
for the firmware pipeline to clear).

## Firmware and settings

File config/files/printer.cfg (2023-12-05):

[include mainsail.cfg]
[include printer/button_macros.cfg]
[include printer/leds.cfg]
[include printer/slicer_macros.cfg]
[include printer/TEST_SPEED.cfg]
[include printer/utility_macros.cfg]

[mcu]
serial: /dev/serial/by-id/usb-Klipper_stm32f446xx_3D0035001050334636383920-if00
restart_method: command

[mcu raspi]
serial: /tmp/klipper_host_mcu

[board_pins]
mcu: mcu
aliases:
    motor0_enable=PF14, motor0_step=PF13, motor0_dir=PF12, motor0_uart=PC4,
    motor1_enable=PF15, motor1_step=PG0,  motor1_dir=PG1,  motor1_uart=PD11,
    motor2_enable=PG5,  motor2_step=PF11, motor2_dir=PG3,  motor2_uart=PC6,
    motor3_enable=PA0,  motor3_step=PG4,  motor3_dir=PC1,  motor3_uart=PC7,
    motor4_enable=PG2,  motor4_step=PF9,  motor4_dir=PF10, motor4_uart=PF2,
    motor5_enable=PF1,  motor5_step=PC13, motor5_dir=PF0,  motor5_uart=PE4,
    motor6_enable=PD4,  motor6_step=PE2,  motor6_dir=PE3,  motor6_uart=PE1,
    motor7_enable=PE0,  motor7_step=PE6,  motor7_dir=PA14, motor7_uart=PD3,

    endstop_x=PG6,
    endstop_y=PG9,
    endstop_tap=PG11,

    temperature_bed=PF3, # TB
    temperature_nozzle=PF4, # T0
    temperature_chamber=PF5, # T1

    heater_nozzle=PA2, # HE0
    heater_bed=PA3, # HE1

    fan_part_cooling=PA8,
    fan_hotend=PE5,
    fan_octopus=PD12,
    fan_raspi=PD13,
    fan_nevermore=PD14,

    led_rgb_stealthburner=PB0,
    led_chamber_illumination=PB10, # HE2

    # EXP1 header
    EXP1_1=PE8,   EXP1_2=PE7,
    EXP1_3=PE9,   EXP1_4=PE10,
    EXP1_5=PE12,  EXP1_6=PE13, # Slot in the socket here
    EXP1_7=PE14,  EXP1_8=PE15,
    EXP1_9=<GND>, EXP1_10=<5V>,

    # EXP2 header
    EXP2_1=PA6,   EXP2_2=PA5,
    EXP2_3=PB1,   EXP2_4=PA4,
    EXP2_5=PB2,   EXP2_6=PA7, # Slot in the socket here
    EXP2_7=PC15,  EXP2_8=<RST>,
    EXP2_9=<GND>, EXP2_10=<5V>,

[printer]
kinematics:     corexy
max_velocity:   500
max_accel:      10000
max_z_velocity: 40
max_z_accel:    350

# Back left
[stepper_x]
enable_pin:              !motor1_enable
step_pin:                motor1_step
dir_pin:                 motor1_dir
rotation_distance:       40
microsteps:              32
full_steps_per_rotation: 400
endstop_pin:             endstop_x
position_min:            0
position_endstop:        250
position_max:            250
homing_speed:            100
second_homing_speed:     25
homing_retract_dist:     5

[tmc2209 stepper_x]
uart_pin:              motor1_uart
interpolate:           false
run_current:           0.8
sense_resistor:        0.110
stealthchop_threshold: 0

# Back right
[stepper_y]
enable_pin:              !motor0_enable
step_pin:                motor0_step
dir_pin:                 motor0_dir
rotation_distance:       40
microsteps:              32
full_steps_per_rotation: 400
endstop_pin:             endstop_y
position_min:            0
position_endstop:        257
position_max:            258
homing_speed:            100
second_homing_speed:     25
homing_retract_dist:     5

[tmc2209 stepper_y]
uart_pin:              motor0_uart
interpolate:           false
run_current:           0.8
sense_resistor:        0.110
stealthchop_threshold: 0

# Z0 stepper (front left)
[stepper_z]
enable_pin:          !motor2_enable
step_pin:            motor2_step
dir_pin:             motor2_dir
rotation_distance:   40
gear_ratio:          80:16
microsteps:          32
endstop_pin:         probe:z_virtual_endstop
position_max:        220
position_min:        -2 # Really bad gantry adjustment might require lower neg numbers
homing_speed:        25
second_homing_speed: 5
homing_retract_dist: 5

[tmc2209 stepper_z]
uart_pin:              motor2_uart
interpolate:           false
run_current:           0.8
sense_resistor:        0.110
stealthchop_threshold: 0

# Z1 stepper (back left)
[stepper_z1]
enable_pin:        !motor3_enable
step_pin:          motor3_step
dir_pin:           !motor3_dir
rotation_distance: 40
gear_ratio:        80:16
microsteps:        32

[tmc2209 stepper_z1]
uart_pin:              motor3_uart
interpolate:           false
run_current:           0.8
sense_resistor:        0.110
stealthchop_threshold: 0

# Z2 stepper (back right)
[stepper_z2]
enable_pin:        !motor4_enable
step_pin:          motor4_step
dir_pin:           motor4_dir
rotation_distance: 40
gear_ratio:        80:16
microsteps:        32

[tmc2209 stepper_z2]
uart_pin:              motor4_uart
interpolate:           false
run_current:           0.8
sense_resistor:        0.110
stealthchop_threshold: 0

# Z3 stepper (front right)
[stepper_z3]
enable_pin:        !motor5_enable
step_pin:          motor5_step
dir_pin:           !motor5_dir
rotation_distance: 40
gear_ratio:        80:16
microsteps:        32

[tmc2209 stepper_z3]
uart_pin:              motor5_uart
interpolate:           false
run_current:           0.8
sense_resistor:        0.110
stealthchop_threshold: 0

[probe]
pin: endstop_tap
z_offset: -0.945
x_offset: 0
y_offset: 0
speed: 20 # mm/s probing speed
activate_gcode:
    {% set PROBE_MAX_TEMP = 150 %}
    {% set CURRENT_TEMP = printer.extruder.temperature %}
    {% set TARGET_TEMP = printer.extruder.target %}

    {% if TARGET_TEMP > PROBE_MAX_TEMP %}
        { action_respond_info('Extruder target temperature of %.1f°C is too high, lowering to %.1f°C' % (TARGET_TEMP, PROBE_MAX_TEMP)) }
        M104 S{PROBE_MAX_TEMP - 5} # Set temp, wait is done at the end
    {% elif CURRENT_TEMP > PROBE_MAX_TEMP %}
        { action_respond_info('Extruder temperature %.1f°C is too high, wait for ~%.1f°C' % (CURRENT_TEMP, PROBE_MAX_TEMP)) }
    {% endif %}
    TEMPERATURE_WAIT SENSOR=extruder MAXIMUM={PROBE_MAX_TEMP}

[safe_z_home]
home_xy_position: 125, 125
speed:            100
z_hop:            10

[extruder]
enable_pin:        !motor6_enable
step_pin:          motor6_step
dir_pin:           !motor6_dir
microsteps:        32
nozzle_diameter:   0.4
filament_diameter: 1.75
heater_pin:        heater_nozzle
sensor_pin:        temperature_nozzle
sensor_type:       Generic 3950
control:           pid
pid_Kp:            24.476  # | Measured via PID_CALIBRATE HEATER=extruder TARGET=260
pid_Ki:            1.483   # |
pid_Kd:            100.965 # |
min_temp:          0
max_temp:          280
rotation_distance: 13.396270810234196
    # ^^^ Extruder calibration goes here. Scale this with
    # extrusion_requested/actually_extruded if actual extrusion doesn’t match
    # requested value.
gear_ratio:        50:17
min_extrude_temp:  200 # Don’t extrude below this temperature
max_extrude_only_distance: 200 # Max extrusion by a single GCode command
max_extrude_cross_section: 1 # So we can paint the nozzle primer line. TODO: Remove this once I have a nozzle brush
pressure_advance:  0.03
pwm_cycle_time: 0.01 # Default is 0.1, but leads to flickering chamber LEDs

[tmc2209 extruder]
uart_pin:              motor6_uart
interpolate:           false
run_current:           0.5
sense_resistor:        0.110
stealthchop_threshold: 0

[heater_bed]
heater_pin:  heater_bed
sensor_pin:  temperature_bed
sensor_type: Generic 3950
max_power:   0.8
min_temp:    0
max_temp:    120
control:     pid
pid_Kp:      50.853  # | Measured via PID_CALIBRATE HEATER=heater_bed TARGET=60
pid_Ki:      1.395   # |
pid_Kd:      463.398 # |

[temperature_sensor chamber]
sensor_type: Generic 3950
sensor_pin: temperature_chamber
min_temp:   10
max_temp:   100

[fan]
pin:             fan_part_cooling
kick_start_time: 1
off_below:       0.1

[heater_fan hotend]
pin:             fan_hotend
max_power:       1.0
kick_start_time: 0.5
heater:          extruder
heater_temp:     50
shutdown_speed:  1

[idle_timeout]
gcode:
    TURN_OFF_HEATERS
    M84 # turn off motors
timeout: 1800 # 30m = 30*60s timeout

[quad_gantry_level]
speed:             250 # mm/s
horizontal_move_z: 10
retries:           5
retry_tolerance:   0.0075
max_adjust:        10
# Corners of the gantry, not the bed! Hence the values way out of bounds of the
# print area
gantry_corners:
   -57,-24
   312, 301
# Probe points
points:
   5,  5
   5,  245
   245, 245
   245, 5

[bed_mesh]
speed:                    250
horizontal_move_z:        10
mesh_min:                 5, 5
mesh_max:                 245, 245
probe_count:              5, 5
zero_reference_position:  125, 125

[bed_mesh default]
version = 1
points =
	  0.031250, 0.020000, 0.025000, 0.028750, 0.033750
	  0.063750, 0.015000, 0.023750, 0.008750, 0.021250
	  0.036250, -0.002500, 0.000000, -0.003750, 0.001250
	  0.018750, -0.020000, -0.001250, -0.008750, 0.001250
	  0.020000, 0.001250, 0.021250, 0.018750, 0.035000
x_count    = 5
y_count    = 5
mesh_x_pps = 2
mesh_y_pps = 2
algo       = lagrange
tension    = 0.2
min_x      = 5.0
max_x      = 245.0
min_y      = 20.0
max_y      = 230.0
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

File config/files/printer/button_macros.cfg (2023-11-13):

[gcode_macro TOOLHEAD_ACCESS]
description: Move toolhead forward for easy access, e.g. filament change.
gcode:
    SAVE_GCODE_STATE NAME=STATE_TOOLHEAD_MOVE
    G90
    G0 X125 Y10 Z80 F4000
    RESTORE_GCODE_STATE NAME=STATE_TOOLHEAD_MOVE

[gcode_macro TOOLHEAD_CENTER]
description: Move toolhead to the center, because it looks cool.
gcode:
    SAVE_GCODE_STATE NAME=STATE_TOOLHEAD_MOVE
    G90
    G0 X125 Y125 Z80 F4000
    RESTORE_GCODE_STATE NAME=STATE_TOOLHEAD_MOVE

[gcode_macro TOOLHEAD_BACK]
description: Move toolhead to the back, out of the way
gcode:
    SAVE_GCODE_STATE NAME=STATE_TOOLHEAD_MOVE
    G90
    G0 X125 Y250 Z80 F4000
    RESTORE_GCODE_STATE NAME=STATE_TOOLHEAD_MOVE

[gcode_macro LIGHT_WHITE]
description: Part illumination: white
gcode:
    SET_LED_TEMPLATE LED=stealthburner INDEX=1 TEMPLATE=stealthburner_temperature_display
    SET_LED LED=stealthburner RED=0 GREEN=0 BLUE=0 WHITE=1 INDEX=2 TRANSMIT=0
    SET_LED LED=stealthburner RED=0 GREEN=0 BLUE=0 WHITE=1 INDEX=3

[gcode_macro LIGHT_VAPORWAVE]
description: Part illumination: red/blue
gcode:
    SET_LED_TEMPLATE LED=stealthburner INDEX=1 TEMPLATE=stealthburner_temperature_display
    SET_LED LED=stealthburner RED=1 GREEN=0 BLUE=0 WHITE=0 INDEX=2 TRANSMIT=0
    SET_LED LED=stealthburner RED=0 GREEN=0 BLUE=1 WHITE=0 INDEX=3

[gcode_macro UNLOAD_FILAMENT]
description: Unload filament
gcode:
    SAVE_GCODE_STATE NAME=UNLOAD_FILAMENT
    M83 ; Relative extruder
    G1 E-100 F4000
    RESTORE_GCODE_STATE NAME=UNLOAD_FILAMENT

[gcode_macro LOAD_FILAMENT]
description: Load filament
gcode:
    SAVE_GCODE_STATE NAME=LOAD_FILAMENT
    M83 ; Relative extruder
    G1 E50 F4000 ; Pull it in quickly, then extrude slowly.
    G1 E50 F300 ; F300 = 5mm/s.
    RESTORE_GCODE_STATE NAME=LOAD_FILAMENT

[gcode_macro RANDOM_COLORS]
description: Random colors for the Stealthburner LEDs
gcode:
    {% for i in range(0, 3) %}
        {% set r = (range(0,100+1) | random) / 100 %}
        {% set g = (range(0,100+1) | random) / 100%}
        {% set b = (range(0,100+1) | random) / 100%}
        SET_LED LED=stealthburner RED={r} GREEN={g} BLUE={b} WHITE=0 INDEX={i+1}
    {% endfor %}

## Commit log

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2022-11-02 Configure dashboard to proof of concept state
    [printer.cfg]
2022-11-03 Add printer.cfg and (untested) config upload/download script
    [printer.cfg]
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2022-11-05 Config entries (especially motor pin aliases)
    [printer.cfg]
2022-11-05 More config, untested. Motors, aliases.
    [printer.cfg]
2022-11-05 Config: heater, probe
    [printer.cfg]
2022-11-05 Live testing incoming
    [printer.cfg]
2022-11-05 Buzz motors, fix one of them. a, b, extruder questionable.
    [printer.cfg]
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2022-11-05 Buzzing, homing
    [printer.cfg]
2022-11-05 Set LED color to R, G, B
    [leds.cfg, printer.cfg]
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2022-11-05 Fans tested
    [printer.cfg]
2022-11-05 Set LEDs simultaneously
    [leds.cfg]
2022-11-05 Test extruder heater; configure PID parameters
    [printer.cfg]
2022-11-05 Add chamber temperature sensor
    [printer.cfg]
2022-11-05 Reverse extruder direction
    [printer.cfg]
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2022-11-05 Add PID parameters for bed heating
    [printer.cfg]
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2022-11-05 TRANSMIT=0 doesn’t work: first LED becomes magenta on boot?!
    [leds.cfg]
2022-11-05 Add Klicky macros (verbatim from Github)
    [klicky-bed-mesh-calibrate.cfg, klicky-macros.cfg, klicky-probe.cfg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]
2022-11-05 Calibrate axes and homing
    [printer.cfg]
2022-11-05 Calibrate extruder
    [printer.cfg]
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2022-11-05 Configure idle timeout explicitly (with default values)
    [printer.cfg]
2022-11-05 Klicky probe, what a ride
    [klicky-probe.cfg, klicky-variables.cfg, leds.cfg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]
2022-11-05 QGL; calibrate Z using CALIBRATE_Z
    [printer.cfg]
2022-11-05 Yank up speeds a bit
    [klicky-variables.cfg, printer.cfg]
2022-11-05 First test print (lol)
    [printer.cfg]
2022-11-05 Try fixing the cube test print to no avail
    [leds.cfg, printer.cfg]
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2022-11-05 Add Z velocity machine limit so Prusa/Super slicer don’t go bonkers with Z0.2 F18000
    [printer.cfg]
2022-11-05 First print done!
    [printer.cfg]
2022-11-06 Add button macros
    [button_macros.cfg, printer.cfg]
2022-11-06 Light macros
    [button_macros.cfg, printer.cfg]
2022-11-06 Add macro to preheat for ABS
    [button_macros.cfg]
2022-11-06 Foam pads, status messages
    [button_macros.cfg]
2022-11-06 Button macros
    [button_macros.cfg]
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2022-11-07 Button macros: save state for moves
    [button_macros.cfg]
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2022-11-08 Fixed broken motor (not sure how though)
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2022-11-11 Add relay to toggle 24V PSU from Raspi
    [printer.cfg]
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2022-11-11 Faster Klicky movements (I should introduce a variable for calibration movements somewhere!)
    [klicky-variables.cfg]
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2022-11-11 Bigger bed mesh contour (not used for calibration yet, bed mesh is still the old one!)
    [printer.cfg]
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2022-11-11 Add nozzle scrub macros (unused)
    [scrub.cfg]
2022-11-11 Increase max extrusion cross section so I can use a primer line
    [printer.cfg]
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2022-11-11 Add PID controlled Raspi, Octopus fans
    PID parameters are pretty arbitrary, need tuning
    [printer.cfg]
2022-11-11 Update position of Klicky probe (installed purge bucket)
    [klicky-variables.cfg]
2022-11-11 Make Raspi/Octopus fans manual for better tuning
    [printer.cfg]
2022-11-11 Preheating ABS: can be done with heater preset, doesn’t need macro
    [button_macros.cfg]
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2022-11-11 Enable exclude_object in Klipper
    [printer.cfg]
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2022-11-13 Macro for random LED colors
    [button_macros.cfg]
2022-11-13 Fix flipped Raspi/Octopus fan outputs
    [printer.cfg]
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2022-11-14 Add custom nozzle wipe macro
    [scrub.cfg]
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2022-11-14 Lower position for tool head access
    [button_macros.cfg]
2022-11-14 260°C for ABS filament loading/unloading
    [button_macros.cfg]
2022-11-14 More filament loading/unloading extrusion distance
    [button_macros.cfg]
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2022-11-15 Macro for moving toolhead oer purge bucket
    [button_macros.cfg]
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2022-11-17 Parameterize nozzle wipe, make it a button
    [button_macros.cfg]
2022-11-17 Auto-control electronics fans (watermark algorithm)
    [printer.cfg]
2022-11-17 Don’t shut off power on error: hotend heatsink needs cooling!
2022-11-17 Enable GCode arcs (G2, G3)
    [printer.cfg]
2022-11-17 Add flow rate measurement attempts (and fix of broken relay)
2022-11-17 Add nozzle flow test macro (still some rough edges!)
    [printer.cfg, utility_macros.cfg]
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2022-11-19 Flipped Octopus/Raspi fans again, woops. Also fan parameter tuning.
    [printer.cfg]
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2022-11-23 Add heat-indicating Stealthburner template
    [leds.cfg]
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2022-11-26 First Z calibration probe: fast (previously disabled to be safe)
    [printer.cfg]
2022-11-26 Filament unload/load macro tweaks
    [button_macros.cfg]
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2022-11-27 Re-enable manual fans again for two reasons:
    1. Less annoying
    2. Some constant air flow for the Octopus is nice to cool the drivers.
    The temperature-controlled fans work based on MCU temperature, but
    the drivers should be cooled regardless.
    [printer.cfg]
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2022-12-02 Add new pressure advance calibration GCode
    [pressure_advance-2022-11-09.g, pressure_advance-2022-11-30.g]
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2022-12-03 Configure chamber LED strips
    [leds.cfg, printer.cfg]
2022-12-03 [Pictures] LED installation, failed hinges
2022-12-03 Increase heater PWM frequency by factor of 10 to avoid flickering LEDs
    [printer.cfg]
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2022-12-07 Buildlog: Z wobble, hinges, extrusion multiplier
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2022-12-07 Default cycle time for PCF (it wasn’t the source of its erratic behavior)
    [printer.cfg]
2022-12-13 Fix wrong sign on hole size compensation
2022-12-13 Fix temperature window waiting type error
2022-12-19 Disable hole size compensation (SuperSlicer might even have a sign error here?)
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2022-12-21 Remove Klicky from config
    [klicky-bed-mesh-calibrate.cfg, klicky-macros.cfg, klicky-probe.cfg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]
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2022-12-21 Macro fine-tuning. Also single pass for QGL.
    [printer.cfg]
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2022-12-22 Tweak homing speeds: faster for XY, more precise second homing for Z
    [printer.cfg]
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2022-12-22 Run hotend fan on shutdown on full throttle
    [printer.cfg]
2022-12-22 Fine-tune first layer (Z offset) with test prints
    [printer.cfg]
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2023-01-10 Reduce minimum Z position to -2, otherwise (tap) probing sometimes fails
    [printer.cfg]
2023-02-17 Minimum Z position -2 so hardcore QGL works
    [printer.cfg]
2023-07-12 Switch to 0.6mm CHT nozzle
    [printer.cfg]
2023-07-12 Back to 0.4mm nozzle
    [printer.cfg]
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2023-11-13 Switch on temperature LED display
    [button_macros.cfg, leds.cfg]
2023-12-05 Replace deprecated bed mesh option […]
    Docs here: http://www.klipper3d.org/Bed_Mesh.html#configuring-the-zero-reference-position
    [printer.cfg]
